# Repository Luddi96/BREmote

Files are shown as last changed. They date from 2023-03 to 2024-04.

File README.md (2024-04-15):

# BREmote - Open Source eFoil and Esk8 remote 
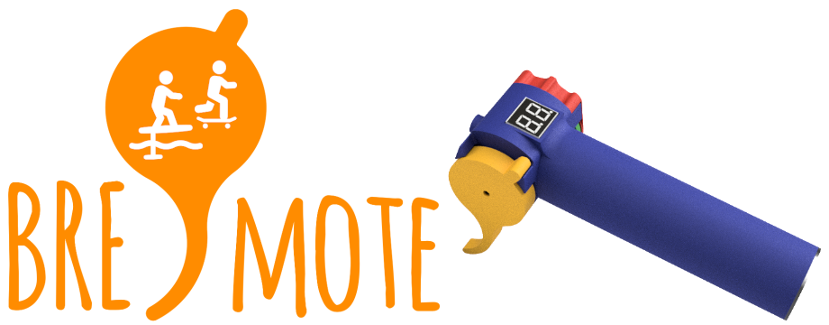
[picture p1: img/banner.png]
Banner


## Features:
* All mechanical parts 3D printed (even the springs)
* Symmetric design - left & right side can be swapped
* Sustainable - All external parts can be replaced
* Open Source: 3D Models, Electronics and Software are GPL3.0
* 2.4GHz Link (range dependant on antenna type, position)
* Communication with VESC via UART / CAN
* Low battery alarm (vibration)
* Water ingress alarm integrated in receiver
* Fall-off detection (not yet implemented)
* Gears / Power Levels / Cruise Control
* Charging and Programming via USB

## Links:
* [Promo Video](https://youtu.be/fF5BHrkHTNA)
* [Overview + Build Video](https://youtu.be/kb76z3FXLc0)
* [Updated Build Video](https://youtu.be/RKn8jVGVD6g)
* [Deep Dive Video](https://youtu.be/cdQ3Ppyngpk)
* [Update Video 04/2023](https://youtu.be/SpBOiRbGKgA)
* [Steering & Long Range Update Video](https://youtu.be/DhPk98Wdcn0)

## Parts needed:
### Electronics:
* [Tx & Rx PCBs, order at JLCPCB, Gerbers see releases](https://github.com/Luddi96/BREmote/releases)
	* [Instruction how to order at JLC (only do Step 2&4)](https://youtu.be/y3GviDr0o1s)
* [Tx wireless module "Color: NRF24L01 SMD"](https://de.aliexpress.com/item/1005004905334589.html)
* [Rx wireless module "Color: GT-24 SMD"](https://de.aliexpress.com/item/1005004905334589.html)
* [IPEX Antenna for Rx](https://de.aliexpress.com/item/1005003399563785.html)
* [0.36" 2-digit, 7-Segment Display, Common Cathode "CC"](https://de.aliexpress.com/item/32730115504.html)
* [2x SMD Header, 2x5-pin](https://de.aliexpress.com/item/32336498109.html)
* [EITHER Connector SP13 4-pin](https://de.aliexpress.com/item/1005001891060229.html)
* [OR Magnetic Connector](https://de.aliexpress.com/item/4001283688823.html)
* [Battery Sanyo UR14500AC 740mAh](https://www.nkon.nl/de/sanyo-ur14500ac-740mah-1-52a-reclaimed.html)
* [Vibration Motor 24x7mm, 3.7 to 5V](https://de.aliexpress.com/item/1005004063804397.html)

### Mechanics:
* [2x Magnet N52 D3x6mm](https://www.ebay.de/itm/162903572491?var=461969545239)
* [2x Self-Threading Screw DIN7982 2.2x6.5mm](https://www.ebay.de/itm/272909463518?epid=17007662352)
* [PU Foam, ~Factor 15, e.g. Talamex 45729200](https://www.boatcareshop.nl/bootverf-bootlak/talamex-pu-schuim-2-componenten-200-cc)
* [3D Printed Parts, see releases](https://github.com/Luddi96/BREmote/releases)

## Recommended Connector Pinning:
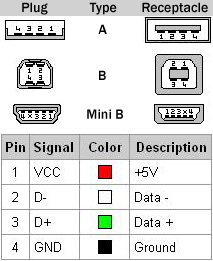
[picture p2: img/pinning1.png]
Pinning1
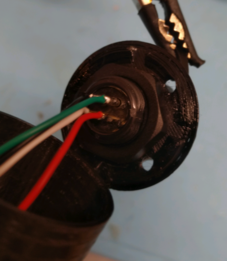
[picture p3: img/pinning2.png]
Pinning2
 

## Usage:
- With the remote off, push the toggle forward to turn it on
- As long as you keep the toggle forward, you will be shown the internal battery capacity in %
- With `//#define NO_LOCK` disabled in SHARED_CONFIG.h:
	- The remote will start in locked state
	- Push the toggle down to unlock
	- The remote will show you "PP", demanding you to push the trigger to its maximum position
	- Once you release the trigger, the remote will be in operating state
	- Push the toggle up/down to increase/decrease gear (The remote will always start in *lowest* gear)
	- Push and hold the toggle down to lock again
	- Push and hold the toggle up to turn off the remote
- With `#define NO_LOCK` enabled in SHARED_CONFIG.h:
	- The remote will immediately start in unlocked state
	- Push the toggle up/down to increase/decrease gear  (The remote will always start in *highest* gear)
	- Push and hold the toggle up to turn off the remote

## Status Codes:
| Symbol | Meaning |
| --- | --- |
| [] |System Locked |
| PP |Press Trigger once to arm |
| L0-L9 |Current "Gear", use Toggle to change |
| UU |Undervoltage, charge Battery |

## Error Codes:
| Err Code | Meaning | Potential Causes |
| --- | --- | --- |
| E3 | Packet Content Invalid | Unexpected data received, probably due to SW error or signal interference |
| E4 | No Ack | No acknowledgement from Receiver, signal too weak or signal interference |
| E5 | EEPROM Error | Unexpected/no calibration in EEPROM, try calibrating the remote again |
| E6 | NRF Module | NRF (Wireless) Module can't be initialized, probably hardware fault |
| E7 | Water Ingress | Water on the water detection electrodes attached to the receiver. This feature can be disabled in code if you dont use it (default: enabled). |
| E8 | BMS Fault | BMS has disabled its output connected to the receiver. This feature can be disabled in code if you dont use it (default: disabled). |

# Connection Examples:

<details>
<summary>VESC with UART</summary>

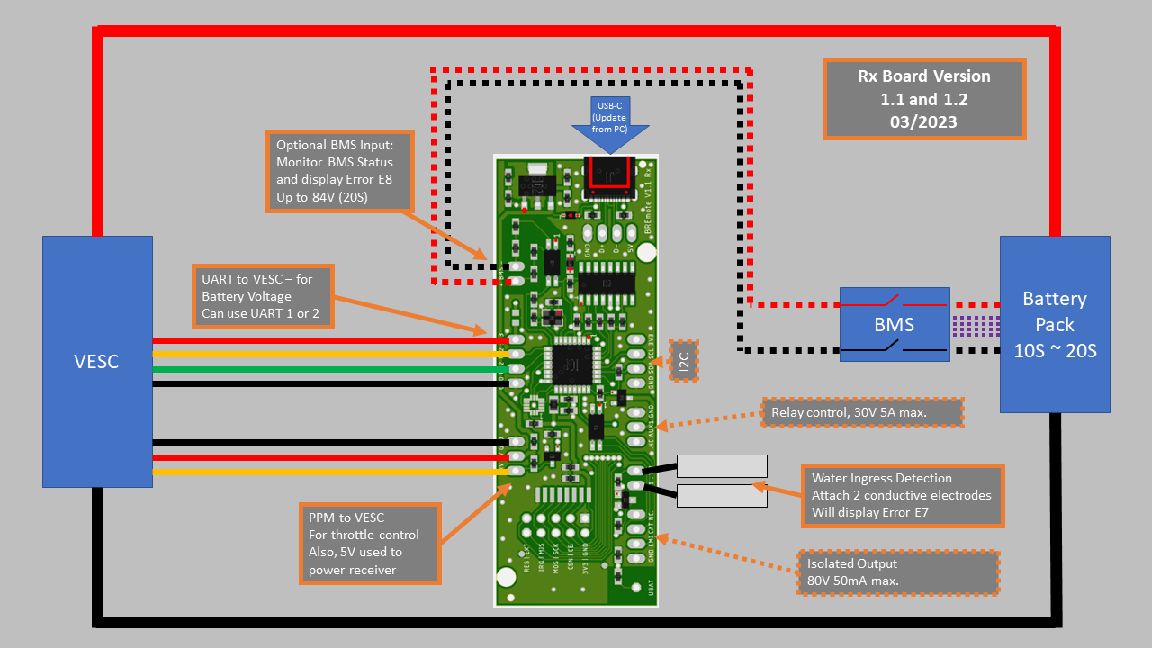
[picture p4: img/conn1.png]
Conn1


</details>

<details>
<summary>ESC or VESC WITHOUT UART</summary>

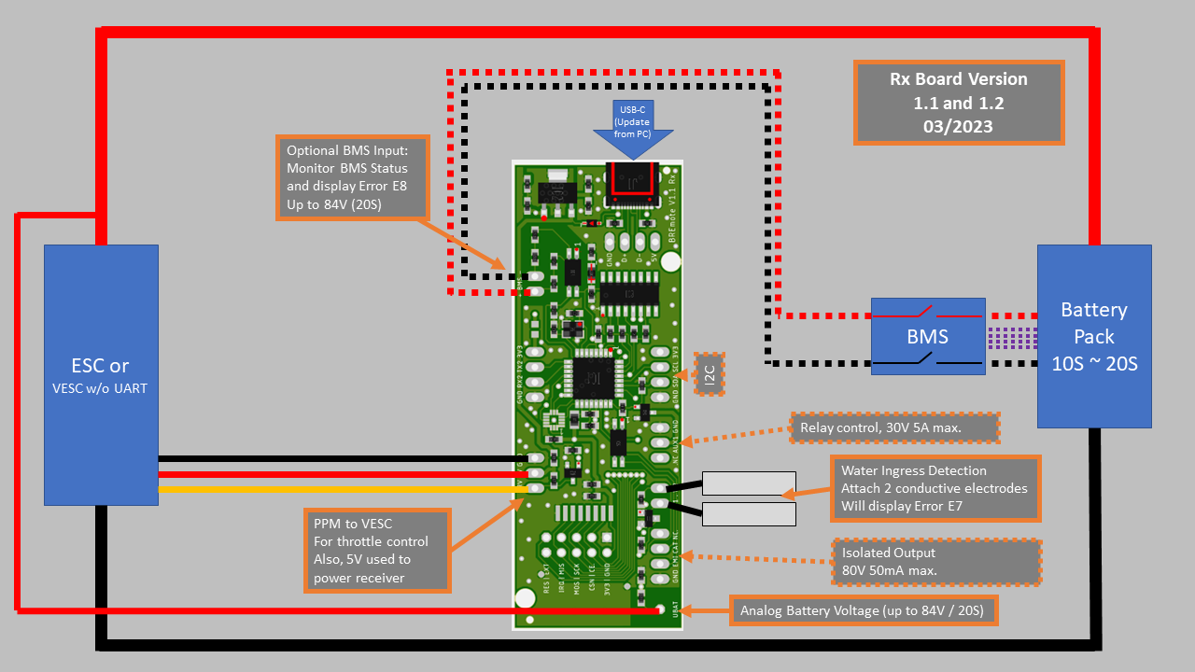
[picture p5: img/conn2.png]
Conn2


</details>

<details>
<summary>Steering/Dual Motor</summary>

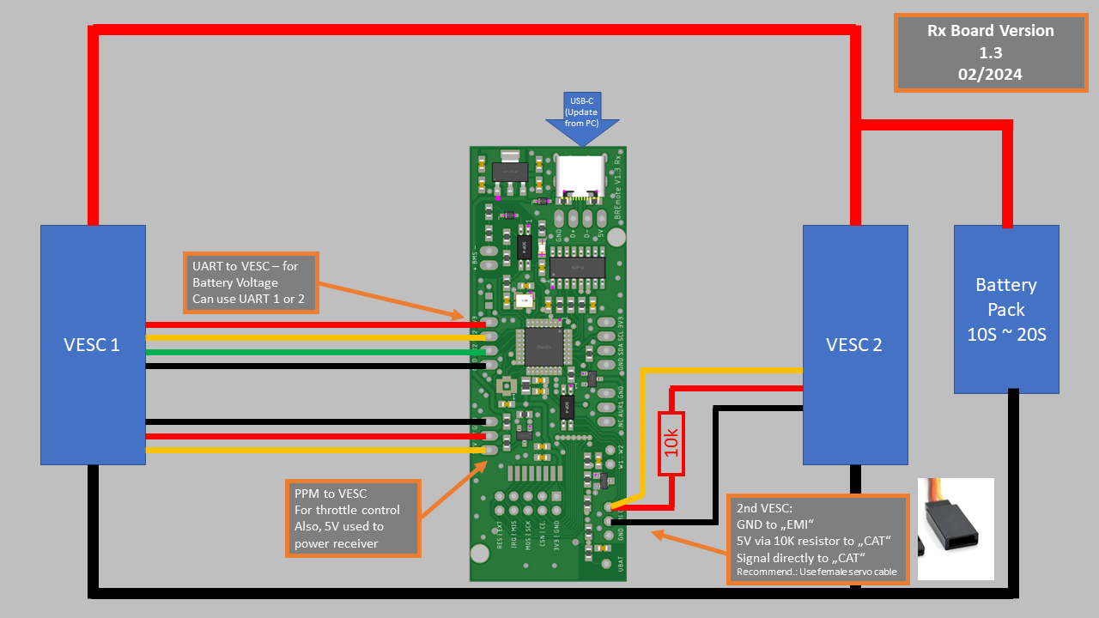
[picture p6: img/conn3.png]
Conn3


</details>

---
# FAQ:
Q: When trying to program the remote with the Arduino IDE, I get an error "avrdude: stk500_getsync()"
A: Make sure you selected "Arduino Nano ATmega328P **(Old Bootloader)**"

---
# Changelog:
### 2024-04-15: [Release V1.7]
Note: Changing to this release will require new calibration!
### 2024-04-15: [Source - all]
- Tx:
	- THR_TO_PWRUP: Remote can be set to only turn on when throttle is pressed (more robust to unwanted turn-on)
	- REVERSE: Instead of 10 forward gears, there is a forward and reverse gear 
	- DONT_SEND_IDLE: Remote will stop sending packets when trigger is not pressed (multiple remotes can be used with one Rx, e.g. for sharing a tow boogie)
- Rx:
	- Diff. Steering
- Calibration:
	- Added new paramter for "THR_TO_PWRUP" function
- Add connection example for Steer/Dual Motor
### 2023-12-28: [Release V1.6.4]
### 2023-12-28: [Mechanics - LR]
- Minor changes on main body
	- Longer antenna hole (now 58mm)
	- Reinforcements
### 2023-06-01: [Release V1.6.3]
### 2023-10-02: [Mechanics - LR]
- Added Juergens improved version of the long range bodies
### 2023-06-01: [Release V1.6.2]
### 2023-10-02: [Source - Tx]
- Softer Gears: When at full throttle, changing gear is smoothened (Thanks to Dyse)
### 2023-07-24: [Source - Readme]
- Added Information how to connnect ISP for LR version
### 2023-06-01: [Release V1.6]
### 2023-06-01: [Source]
- Remove Toto Mode
- Add more options to customize UI:
	- NO_LOCK
	- NO_POWERBUTTON
	- NO_GEARS
- Add temperature display
### 2023-05-05: [Release V1.5.1]
### 2023-05-05: [Source - Tx]
- Added "Toto mode" (less filtering for another throttle sensing concept)
- Disable Lock & Poweroff when riding (when throttle is engaged)
### 2023-04-23: [Release V1.5]
### 2023-04-23: [Source]
- Added Steering Function (see [update video](https://youtu.be/DhPk98Wdcn0) )
### 2023-04-23: [Electronics - Tx]
- Added longrange (LR) version of Tx board (uses same NRF module like Rx)
### 2023-04-14: [Release V1.4.2]
### 2023-04-14: [Source]
- Set MOSI Pin to "Input" in standby (Critical fix, as this could damage battery)
### 2023-04-14: [Source]
- Add compiler error if address is not changed
- Increase tolerances on some values
### 2023-04-14: [Release V1.4.1]
### 2023-04-14: [Source - Rx]
- Increased NRF interrupt-to-readout delay
### 2023-03-31: [Release V1.4]
### 2023-03-31: [Readme]
- Added connection diagrams
### 2023-03-31: [Source]
- Made connection to VESC UART optional (defined in SHARED_CONFIG)
- Added analog UBAT measurement
### 2023-03-31: [Electronics - Rx]
- Added component to make analog UBAT measurement more resitant to electromagnetic disturbance
### 2023-03-30: [Source]
- Add error timeout, to allow user to change gear during an error
### 2023-03-12: [Release V1.3]
### 2023-03-20: [Electronics - Rx]
- Added components to make Water Ingress Detection (Wetness Sensor) more resitant to electromagnetic disturbance
### 2023-03-20: [Source]
- Added BMS monitoring function
- Fixed Water Ingress Detection (Wetness Sensor) functionality
### 2023-03-12: [Release V1.2]
### 2023-03-12: [Source]
- Added more information, which Board and Processor to select for programming with Arduino IDE
- Renamed Source Files to not contain Version anymore
- Added Water Ingress Detection (Wetness Sensor) functionality
### 2023-03-07: [Release V1.1]
### 2023-03-04: [Electronics - Tx]
- Made Board 1mm smaller (each 0.5mm from top/bottom)
- Therefore shifted SPI vias and some other traces, changed style of motor pinheaders
### 2023-03-04: [Source]
- Found a error which depleated the battery in standby mode.
- Changed System.ino : disablePower() routine
### 2023-01-20: [Mechanics]
- Added Trigger Opitions with -15 and -30°
- Made Selector Rotator and Selector Spring thinner
- Updated "AllTheSmallThings"
### 2022-12-30: [Mechanics]
- Added Trigger spring with 1mm thickness (before: 1.2mm could lead to spring not being able to "roll in" all the way)
### 2022-12-02: [Electronics - Rx]
- Added protection diode to BMS measurement
### 2022-11-06: [Electronics - Tx]
- Better GND Connection for NRF Module
- Corrected Battery Polarity in whiteprint
- Added Diode to VREF
- Changed Reset to SMD Pad

---
# Credits:
Logo uses "watersport" and "Skate" by Adrien Coquet from https://thenounproject.com/. CC BY 3.0.

Thanks to Daniel for implementing and testing the magnetic connector!
Tanks to Dyse for implementing the soft gears feature!
Thanks to Juergen for the improved long range bodies!

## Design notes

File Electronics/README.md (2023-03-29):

## Note:
Before soldering NRF Module in Place, upload Bootloader to Boards. For that, see Source Readme.

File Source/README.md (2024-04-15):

## How to upload bootloader
Before you can use Arduino IDE to flash the firmware, you need to upload the bootloader to the BREmote once!
For that, you need an AVR ISP or another Arduino.

Note: You should do this, before soldering the NRF Module in place. Just take 6 wires and solder them directly to the pads. Upload bootloader and verify success. Afterwards, desolder the wires and solder NRF module into place.

Note: If you have the accelerometer populated, flashing should be done at 3.3V (Arduino has 5V), you should use a level shifter on all SPI pins to avoid damage to the accelerometer IC.

Note: The Pinout is only valid for the "normal" Tx Version. For the Tx_LR (long range), please contact me.

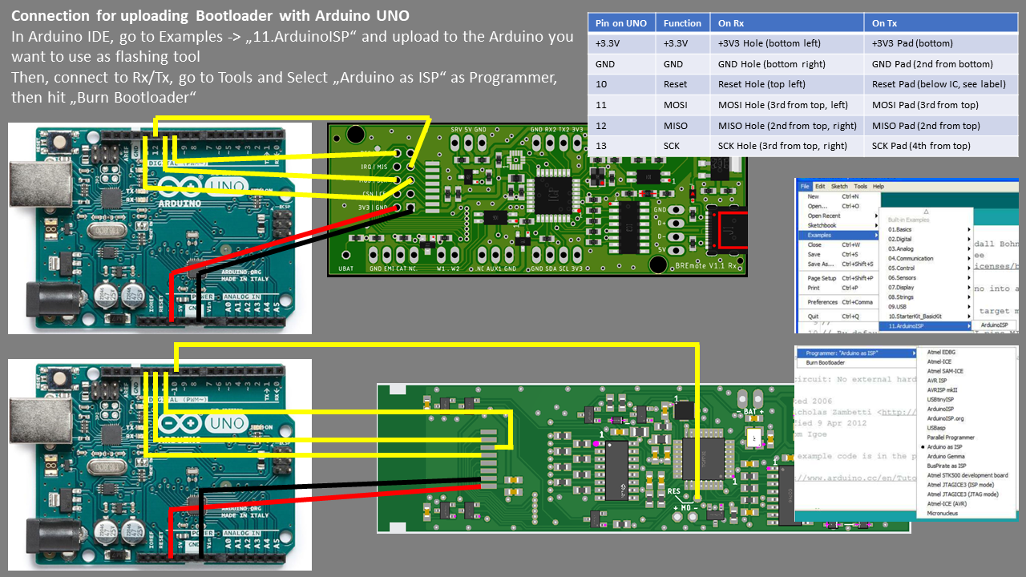
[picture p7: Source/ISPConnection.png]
ISP

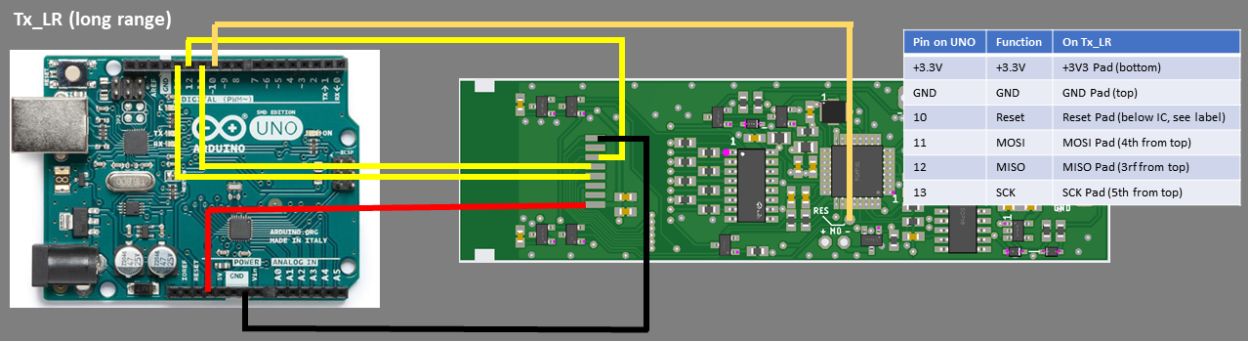
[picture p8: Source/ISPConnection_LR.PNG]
ISP_LR


## How to compile / upload

Download Arduino IDE.
In Arduino IDE, go to Sketch -> Add Library -> Search for "RF24" and Install "RF24" from TMRh20 (you'll need to scroll down a bit).

Board

If the upload does not work, select as Board "Arduino Nano (ATMEGA328P) (OLD BOOTLOADER)"

## Software Changes
These are the most frequent changes in "SHARED_CONFIG.h":
Change this in BOTH the Tx and Rx directory!
```
uint8_t rxAddr[6] = {"BREAI"}; //From Rx To Tx (Board to Remote)
uint8_t txAddr[6] = {"BREAO"}; //From Tx To Rx (BRemote to Board)
```
* For the adresses, choose any 5-character strings you want. Make sure it is unique for everybody using a BREmote at the same time.
```
#define NO_LOCK
```
* If "NO_LOCK" is uncommented, the remote will start locked and with Powerlevel 0 as default. "NO_LOCK" will deactivate locking & start at Powerlevel 9.
```
#define FOIL_BAT_EMPTY_AT 180 //10*V (e.g. 200 = 20V)
#define FOIL_BAT_FULL_AT 220  //10*V (e.g. 200 = 20V)
```
* "FOIL_BAT_xx" will define at which voltage the VESC battery is recognized as full or empty.
This change is made in the config of Rx! DO NOT change the INT_VBAT_xx in Tx!
This is in 10*Voltage, Example values (2.5V/4.2V):

| Series Pack | EMPTY_AT | FULL_AT |
| --- | --- | --- |
| 10S | 250 | 420 |
| 12S | 300 | 504 |
| 14S | 350 | 588 |
| 16S | 400 | 672 |
| 18S | 450 | 756 |
| 20S | 500 | 840 |

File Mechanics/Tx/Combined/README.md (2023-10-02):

## Print settings:
- All parts are already in correct orientation for printing!
- Only Main_Body needs support.
- Nozzle Dia 0.4mm
- Layer Height 0.2mm
- First Layer 0.3mm
- 3 outer layers
- PETG recommended.

## What to do:
- Print "AllTheSmallThings", Handle, MainBodies.
- Trigger:
	- There are 3 trigger angles, see image below
	- Righthander: Print Trigger once
	- Lefthander: Mirror Trigger and print once
- Print "AllTools" for easier assembly

These are the different trigger angles:
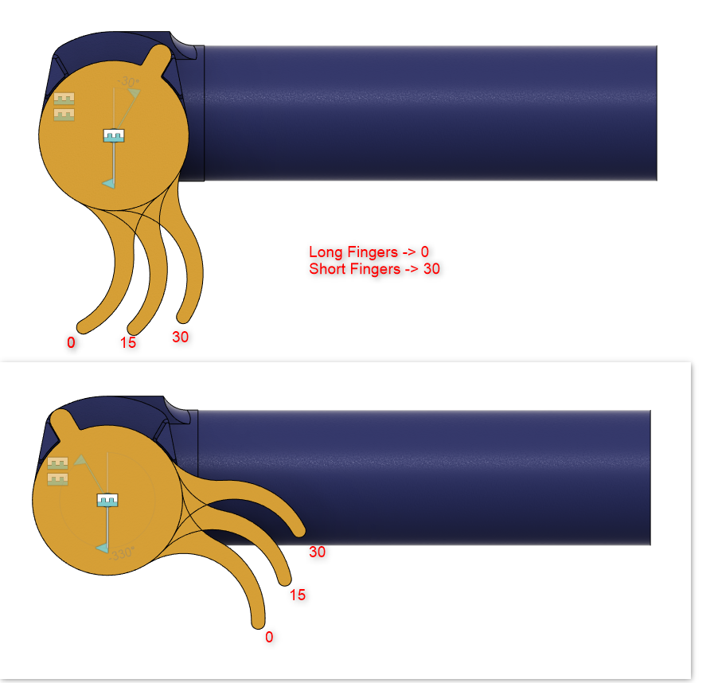
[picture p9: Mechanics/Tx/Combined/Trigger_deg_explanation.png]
Image of different trigger angles


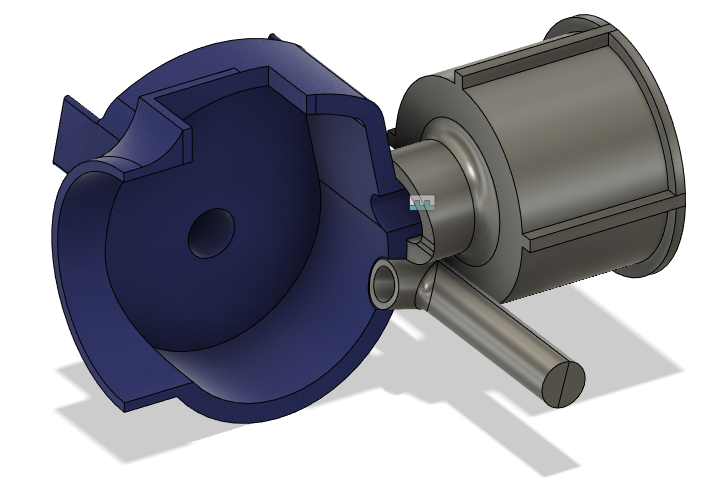
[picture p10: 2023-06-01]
Mechanics/Tx/Long_Range/2023-05-06_13h26_05.png

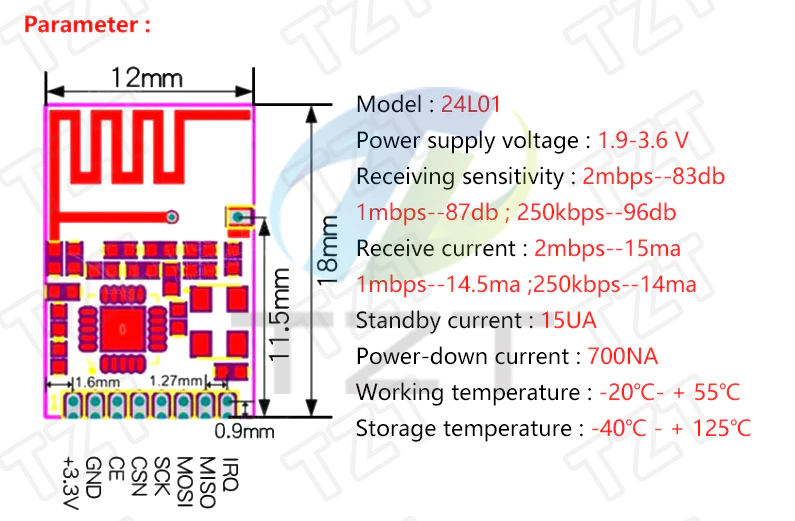
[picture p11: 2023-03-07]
Electronics/Datasheets/Tx_Module.png

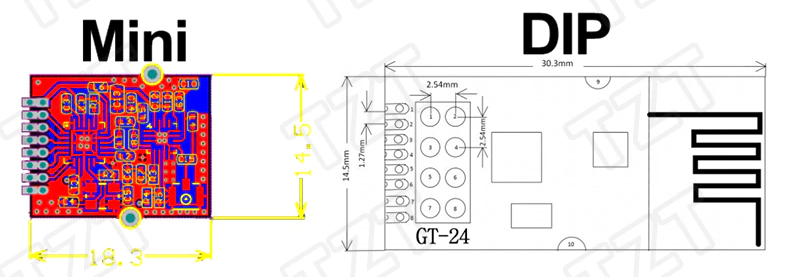
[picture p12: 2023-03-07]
Electronics/Datasheets/Rx_1.png

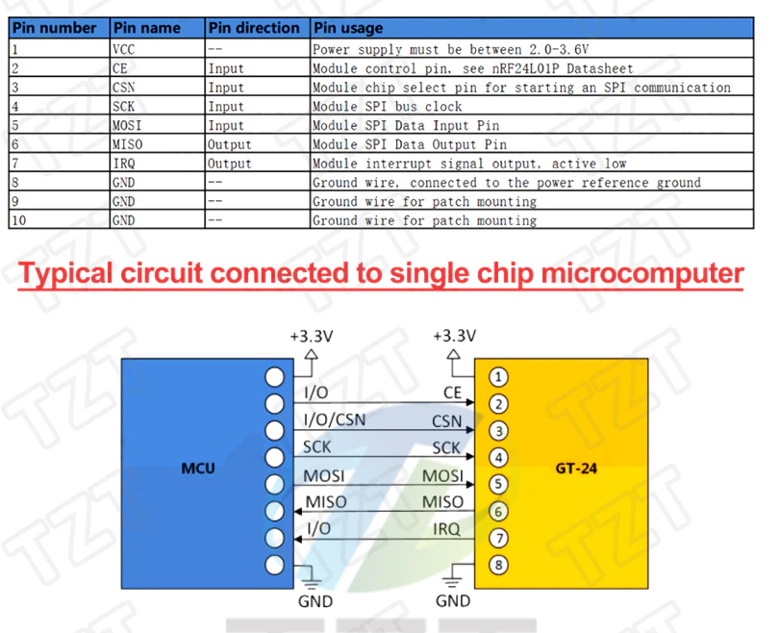
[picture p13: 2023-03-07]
Electronics/Datasheets/Rx_2.png

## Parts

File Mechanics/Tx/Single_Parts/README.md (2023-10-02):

## Print settings:
- All parts are already in correct orientation for printing!
- Only Main_Body needs support.
- Nozzle Dia 0.4mm
- Layer Height 0.2mm
- First Layer 0.3mm
- 3 outer layers
- PETG recommended.

## What to do:
- Parts without numbers at the end, print 1 times
- Parts with _2x, print 2 times
- Parts with _2m, print once and once mirrored (MagRodCover and MainBody)
- For the MagRodStopper, there are 4 lenghts, try with _+02_default
	- If too tight -> use _+04, if too lose -> use _00 or _-02
- Trigger:
	- There are 3 trigger angles, see image below
	- Righthander: Print Trigger once
	- Lefthander: Mirror Trigger and print once
- Or just use the combined .stl in the "Combined" folder

These are the different trigger angles:
Image of different trigger angles

Special thanks to Daniel for designing and testing the "HandleBackCap_Mag"

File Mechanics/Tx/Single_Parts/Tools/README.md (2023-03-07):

Note: Please remove AssemblyHelper Top and Bottom after glueup (they don't belong on the final remote)

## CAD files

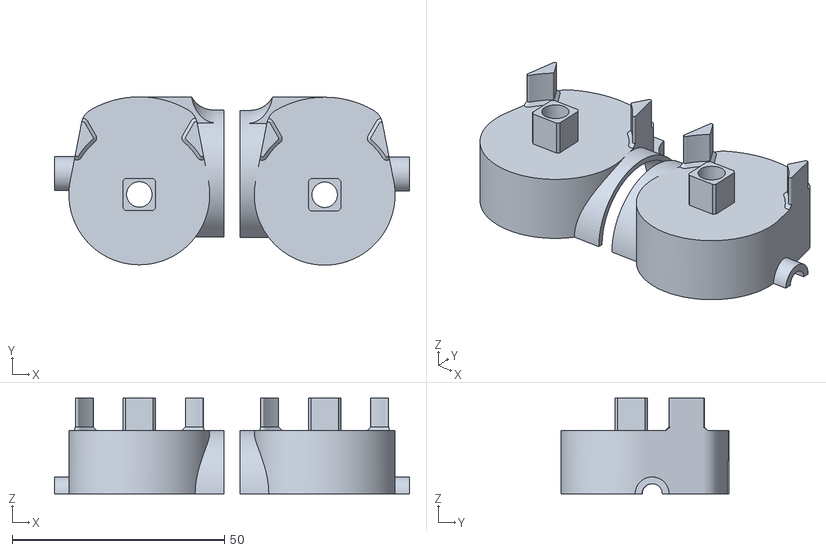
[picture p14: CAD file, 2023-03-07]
Mechanics/Tx/Combined/MainBodies.stl
83.7 x 39.7 x 22.6

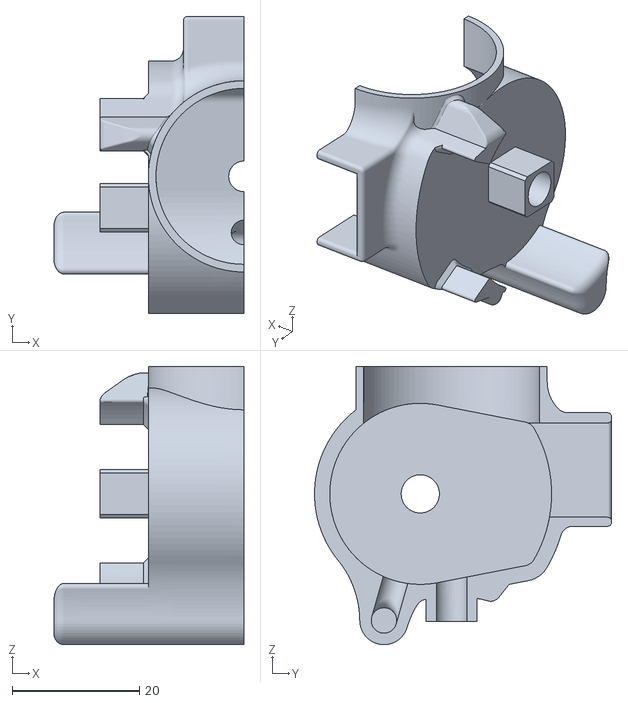
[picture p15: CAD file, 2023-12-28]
Mechanics/Tx/Long_Range/main_body_left_normal.stl
29.8 x 46.6 x 43.7

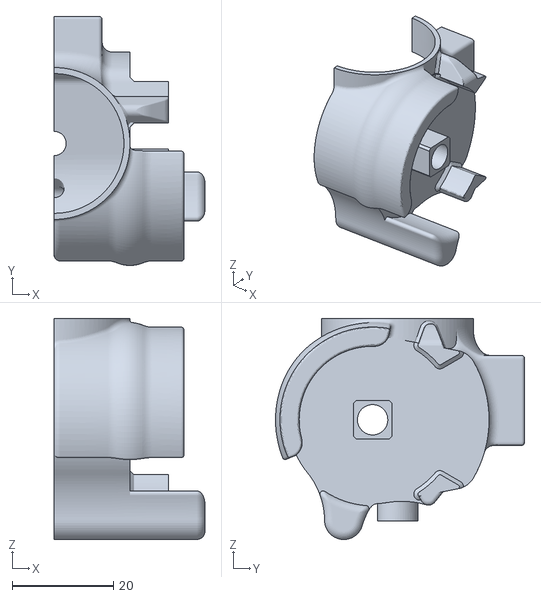
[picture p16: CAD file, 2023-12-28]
Mechanics/Tx/Long_Range/main_body_right_toggle_protection.stl
29.8 x 49.2 x 43.7

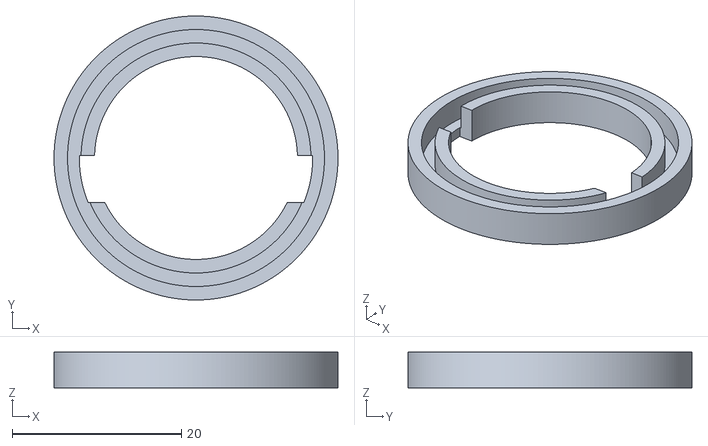
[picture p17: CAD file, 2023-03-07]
Mechanics/Tx/Single_Parts/Tools/AssemblyHelperBottom.stl
33.6 x 33.6 x 4.20

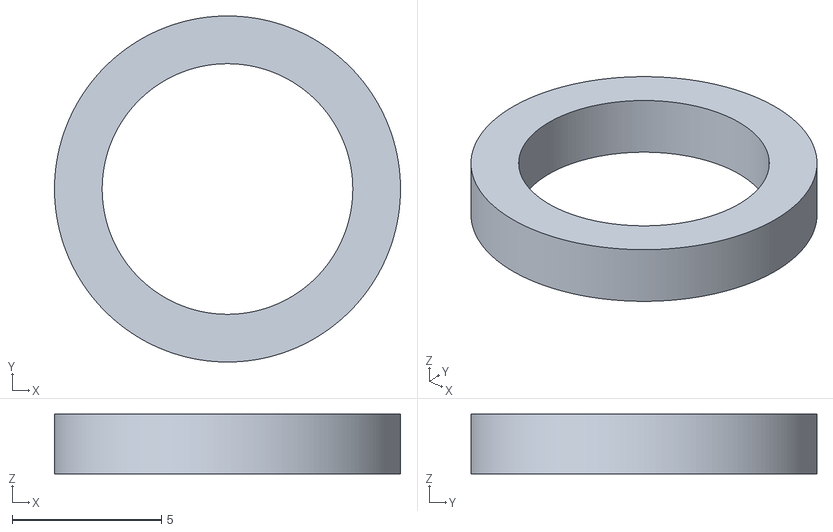
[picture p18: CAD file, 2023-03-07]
Mechanics/Tx/Single_Parts/Tools/AssemblyHelperTop.stl
11.6 x 11.6 x 2.00

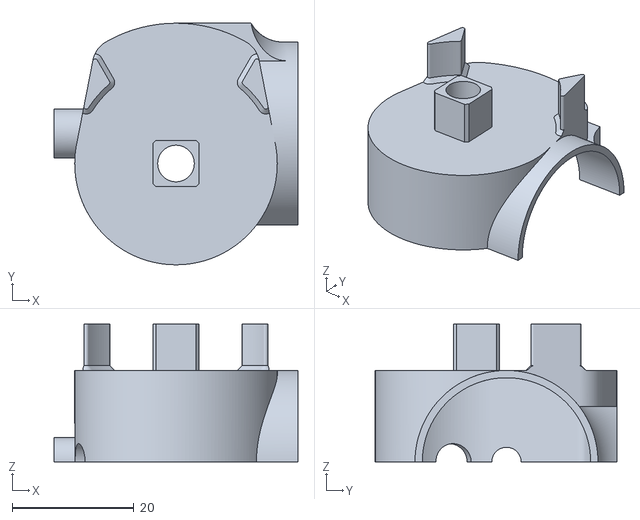
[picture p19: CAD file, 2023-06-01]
Mechanics/Tx/Long_Range/MainBody_Left_2m.stl
40.0 x 39.6 x 22.6

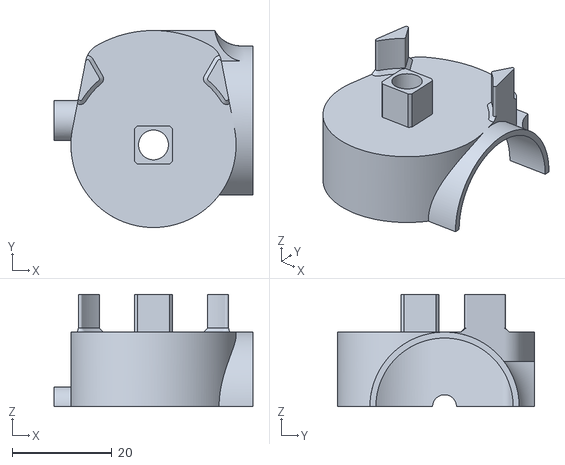
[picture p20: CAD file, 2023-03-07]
Mechanics/Tx/Single_Parts/MainBody_Left_2m.stl
40.0 x 39.6 x 22.6

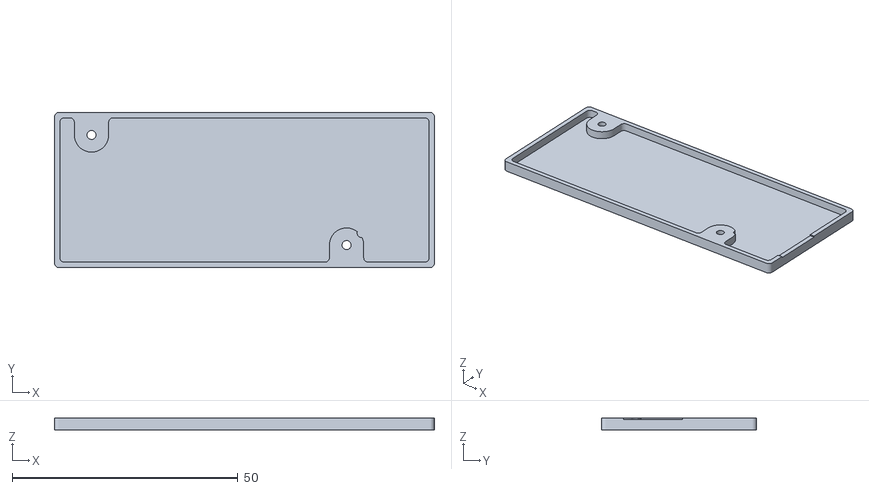
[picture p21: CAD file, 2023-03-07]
Mechanics/Rx/Bottom.stl
84.2 x 34.4 x 2.70

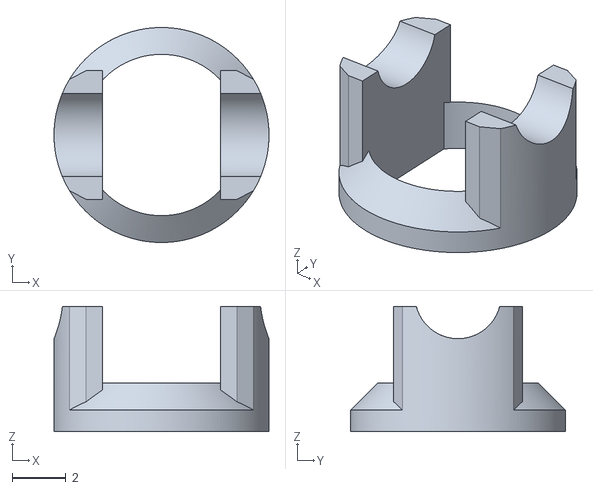
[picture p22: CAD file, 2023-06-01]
Mechanics/Tx/Single_Parts/MagRodStopper_00_less_2x.stl
8.00 x 8.00 x 4.66

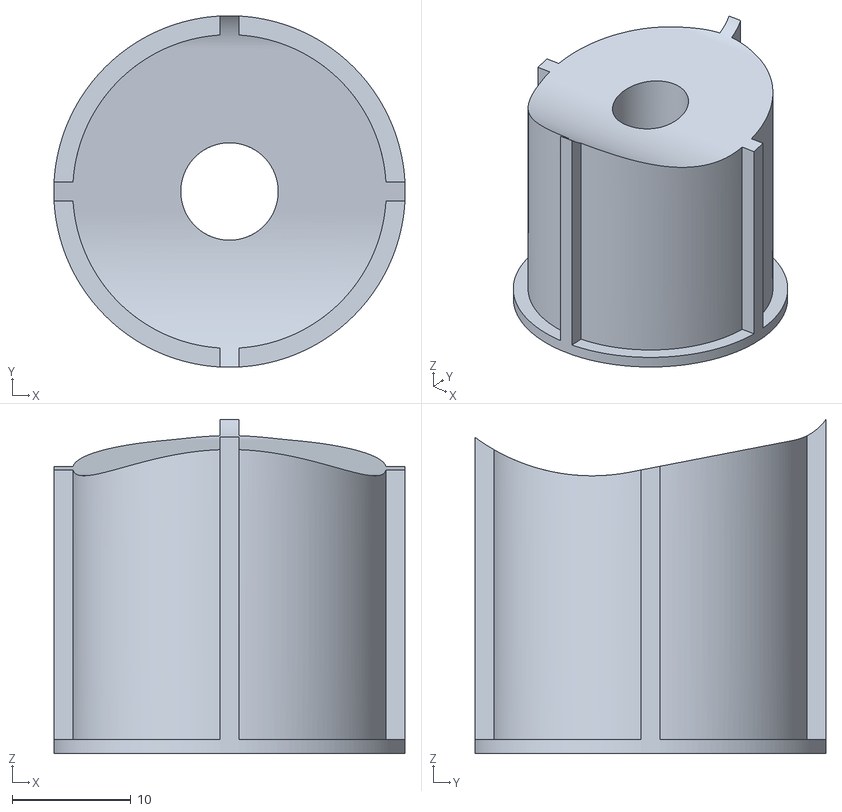
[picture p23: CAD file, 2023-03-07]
Mechanics/Tx/Single_Parts/Tools/PushRod.stl
29.6 x 29.6 x 28.2

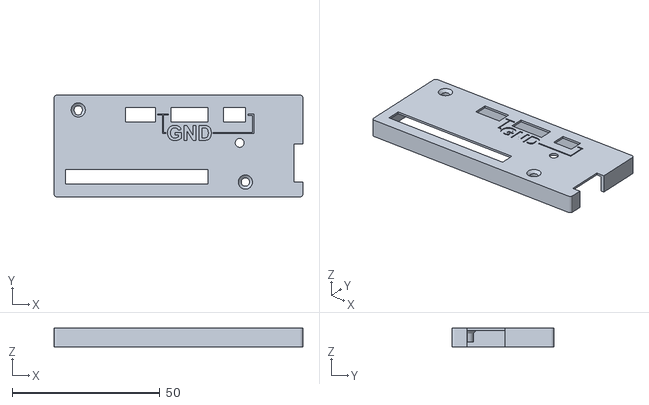
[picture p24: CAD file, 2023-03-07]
Mechanics/Rx/Top.stl
84.2 x 34.4 x 6.27

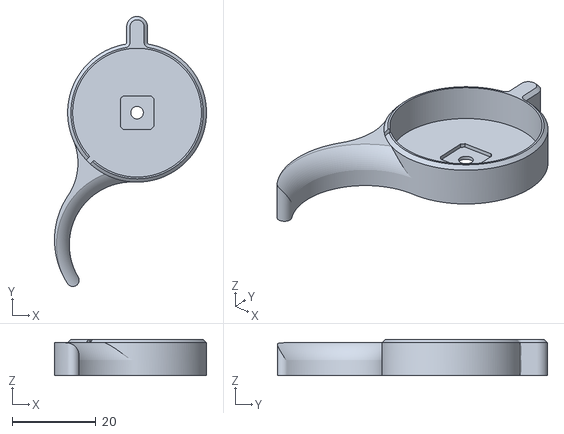
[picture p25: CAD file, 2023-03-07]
Mechanics/Tx/Combined/Trigger_0deg.stl
36.3 x 64.6 x 8.70

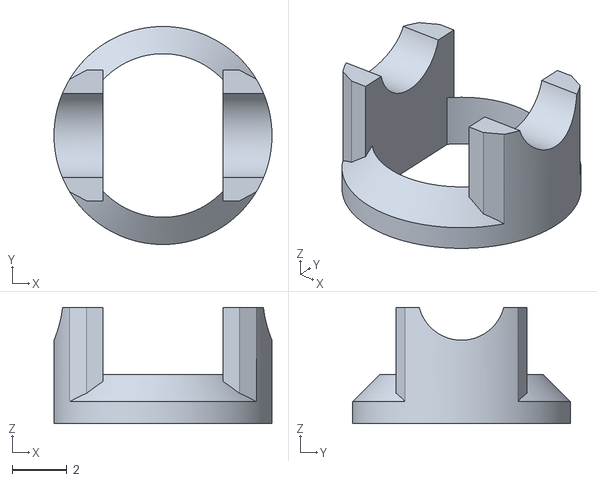
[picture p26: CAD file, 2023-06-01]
Mechanics/Tx/Single_Parts/MagRodStopper_+04_more_2x.stl
8.00 x 8.00 x 4.26

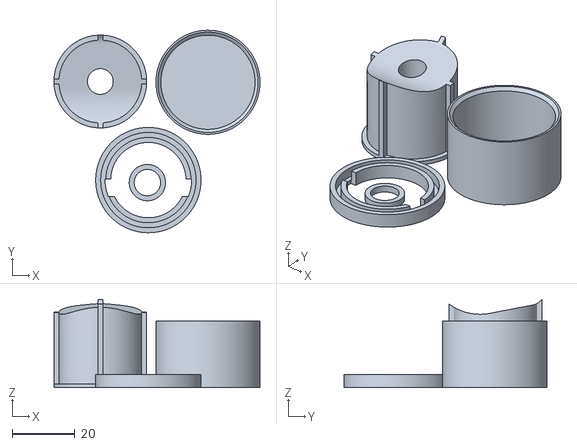
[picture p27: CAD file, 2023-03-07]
Mechanics/Tx/Combined/AllTools.stl
65.7 x 64.6 x 28.2

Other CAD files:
Mechanics/Tx/Long_Range/Special_Pushrod.stl
Mechanics/Tx/Single_Parts/MagRodStopper_-02_less_2x.stl
Mechanics/Tx/Single_Parts/Tools/MixCup.stl
Mechanics/Tx/Combined/Handle.stl
Mechanics/Tx/Combined/AllTheSmallThings.stl
Mechanics/Tx/Combined/Trigger_15deg.stl
Mechanics/Tx/Combined/Trigger_30deg.stl
Mechanics/Tx/Long_Range/Antenna1.stl
Mechanics/Tx/Long_Range/Antenna2.stl
Mechanics/Tx/Long_Range/old_design/Antenna1.stl
Mechanics/Tx/Long_Range/old_design/Antenna2.stl
Mechanics/Tx/Single_Parts/FillportCover.stl
Mechanics/Tx/Single_Parts/HandleBackCap_Mag.stl
Mechanics/Tx/Single_Parts/HandleBackCap_SP13.stl
Mechanics/Tx/Single_Parts/Handle_100mm.stl
Mechanics/Tx/Single_Parts/MagRodCover_Left_2m.stl
Mechanics/Tx/Single_Parts/MagRodStopper_+02_default_2x.stl
Mechanics/Tx/Single_Parts/MagRod_2x.stl
Mechanics/Tx/Single_Parts/SelectorArm_Bothsides.stl
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

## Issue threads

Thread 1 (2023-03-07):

[Feature Request]: Implement water ingress detection into Rx Source

Luddi96, 2023-03-07:
TODO: Use the existing pin designed for water ingress detection, read it out and send it via the error code byte to the Remote

Luddi96, 2023-03-12:
Resolved in 9b4daf09fd37b46db3c2a3dd7a2333e4f6e3bf7d

Closed 2023-03-12.

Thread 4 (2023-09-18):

[FEATURE REQUEST]: Autopilot

jensutbult, 2023-09-18:
Use the IMU in the RX to steer e.g a tow boogie. Instead of controlling differential thrust or a rudder with the remote, using the select button on the remote will change the heading which the autopilot use to steer the tow boogie. The speed of change of heading will preferably be proportional to how far you pull the lever. By default the autopilot will be off to allow for normal steering via the tow line but as soon as the user turns the select button while throttle is on it will be engaged. The autopilot is disengaged when the throttle is turned to zero again.

This will make it a lot easier to use a tow boogie in waves or simply to practice pumping in flat water. When the user wants to let go of the tow boogie he simply turns the select button while the tow boogie is running. This will engage the autopilot and the tow boogie will keep tracking straight even if waves or wind tries to knock it off course. If the user wants to adjust the heading of the tow boogie steering works very similar to the current implementation but instead of controlling a rudder it will update the internal heading to which the autopilot is trying to steer.

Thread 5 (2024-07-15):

[BUG]: UART not working with VESC 6.0.2 and MKS 75200

patatman, 2024-07-15:
**Describe the bug**
When enabling UART I'm getting the error in the serial monitor:
`Message Error`

For some reason UART won't work. I've soldered TX2 and RX2 to the corresponding RX2 and TX2 on the Bremote receiver, but it won't work.
I've now directly connected the battery to the Receiver so I can see the battery % anyway.

But UART would be intresting, since I can also monitor temperature.

Any idea what it could be?
I've wired the TX to RX and RX to TX.
Baudrate is at 15200

Luddi96, 2024-07-15:
Try connecting TX to TX, Rx to Rx. Please report back if that works.

patatman, 2024-08-25:
Sorry I never responded, I fixed it by using the PPM.
So didn't get around resoldering it. You can close this if you'd like.
Won't be until the winter until I start switching components again

Luddi96, 2024-08-25:
No problem. I will close and you can open a new one should the problem persist

Closed 2024-08-25.

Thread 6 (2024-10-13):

Standard arduino for receiver?

yifeim, 2024-10-13:
Hi,

For people who burned their receivers due to voltage spikes, is it possible to rebuild the receiver using standalone arduino-nano + gt-24 parts? I just need the basic functions to convert radio signal to pwm. Also, I would like to use a separate power source to avoid voltage spikes from the motor end. Thanks!

Luddi96, 2024-10-13:
Hey,
That is possible in principle
However a normal Arduino runs on 5V, the GT24 needs 3.3V so you will have to either add a level shifter or convert the Arduino to 3.3V
Also the PWM output needs a transistor and a few additional components.
You can check out the schematic and compare with an Arduino to see what needs to be added or changed

yifeim, 2024-10-13:
Thank you. Which file should I look at and what software to open it with?

Luddi96, 2024-10-13:
In the Schematic folder, download the .sch file
It can be viewed with Autodesk Eagle or a free online viewer like this one
https://www.pcbway.com/tool/ElectronicDesignViewer

yifeim, 2024-10-14:
Thank you! It's definitely interesting to read through the designs. I think
it might be possible to drive the esc pwm directly through the controller
pin (with some software inversion logic) and, as for 3.3v, we can add a
small led as a power step.

FYI, my board healed itself despite missing the accelerometer, so I am
replying just to learn.

LudwigBre ***@***.***> 于2024年10月13日周日 13:28写道：

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

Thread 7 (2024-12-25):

[FEATURE REQUEST] Temperature allert

StefanGas, 2024-12-25:
I have my ECS in the same box like the receiver.
The ESC has a temperature shutdown at 100°C.
This is suitable for drones and aircrafts with good air cooling but not inside the same box like the battery.
An early temperature allert would be great to know that the temperature in the box is rising and I should give it some time to cool down.
(I use no BMS and I did not found a way to set the temperature for the ESC lower)

I hope that some of the fancy chips on the receiver board has a temperature sensor on board 😁

Luddi96, 2024-12-25:
Hey there,
I can add this in the future
Until then you can add it yourself

Go to the System.h file of the TX firmware
All the way in the end you should see the following

`void checkBattery()
{
  calcInternalBattery();
  if(internal_battery < 20)
  {
    blinkDot |= 0x01;
  }
  else
  {
    blinkDot &= 0xFE;
  }

  if(vesc_battery < FOIL_VBAT_WARN_AT)
  {
    blinkDot |= 0x02;
  }
  else
  {
    blinkDot &= 0xFD;
  }

  if(internal_battery < 10)
  {
    poweroff = 1;
  }
}`

Modify the 2nd last if() like following (the value 80 is the desired temperature in °C)
To test if it works first set it to 20°C or something and see if the alarm goes off

if(vesc_battery < FOIL_VBAT_WARN_AT **|| vesc_temp > 80**)

StefanGas, 2024-12-26:
Hi,thanks for the quick reply.Is it possible to measure the temperature in the box with the receiver?I don't have a VESC.Best regards--Am 25.12.24, 18:19 schrieb LudwigBre ***@***.***>:

Hey there,
I can add this in the future
Until then you can add it yourself
Go to the System.h file of the TX firmware
All the way in the end you should see the following
`void checkBattery()
{
calcInternalBattery();
if(internal_battery < 20)
{
blinkDot |= 0x01;
}
else
{
blinkDot &= 0xFE;
}
if(vesc_battery < FOIL_VBAT_WARN_AT)
{
blinkDot |= 0x02;
}
else
{
blinkDot &= 0xFD;
}
if(internal_battery < 10)
{
poweroff = 1;
}
}`
Modify the 2nd last if() like following (the value 80 is the desired temperature in °C)
To test if it works first set it to 20°C or something and see if the alarm goes off
if(vesc_battery < FOIL_VBAT_WARN_AT || vesc_temp > 80)

—Reply to this email directly, view it on GitHub, or unsubscribe.You are receiving this because you authored the thread.Message ID: ***@***.***>

Luddi96, 2024-12-27:
Not without adding an additional sensor and quite a bit of code

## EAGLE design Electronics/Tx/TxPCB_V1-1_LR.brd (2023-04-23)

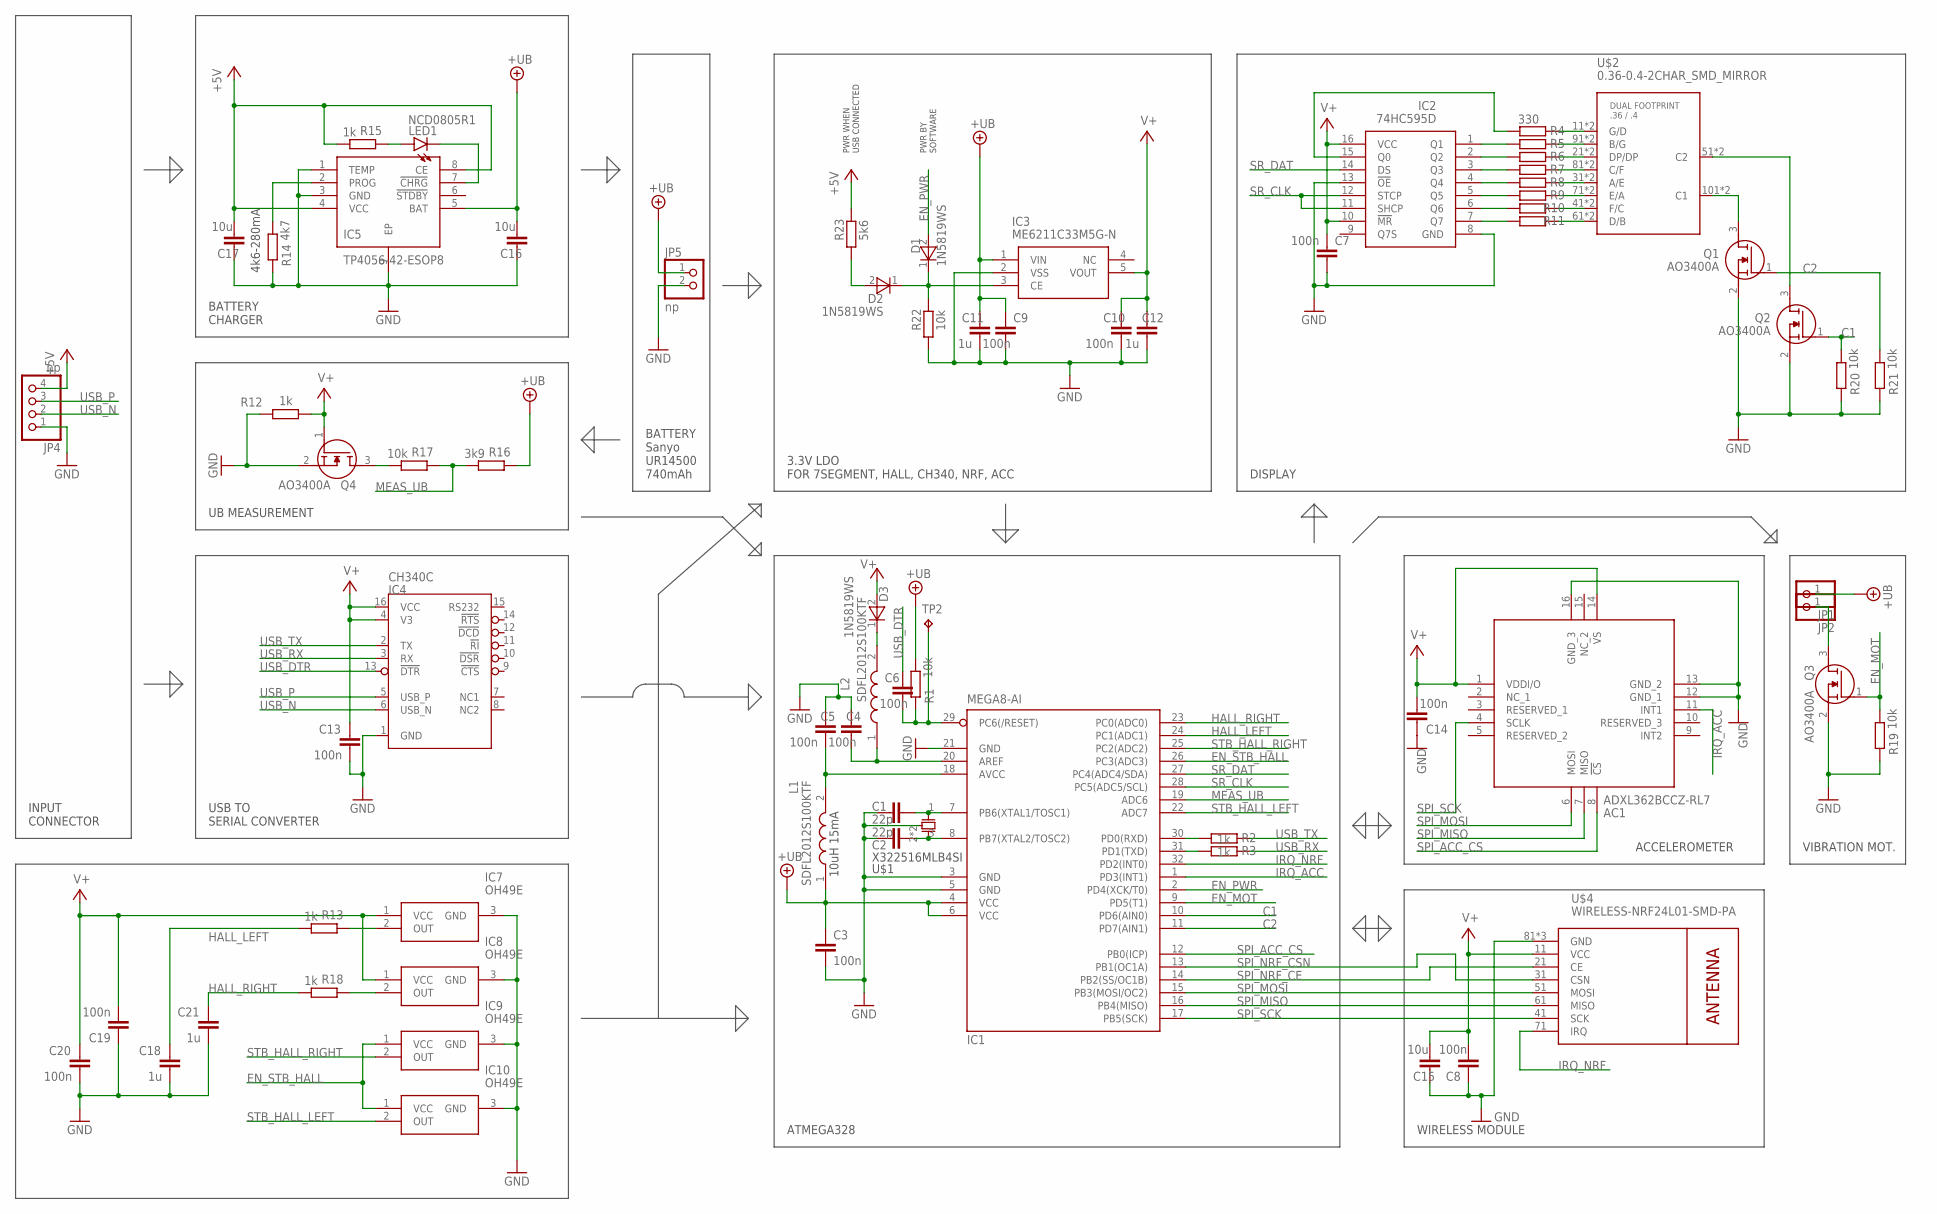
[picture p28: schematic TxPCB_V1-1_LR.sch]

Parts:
AC1: ADXL362BCCZ-RL7; CC-16-4
C1, C2: 22p; C0603
C3, C4, C5, C6, C7, C8, C9, C10, C13, C14, C19, C20: 100n; C0603
C11, C12, C18, C21: 1u; C0603
C15, C16, C17: 10u; C0603
D1, D2, D3: 1N5819WS; SODFL2512X90N
IC1: MEGA8-AI; TQFP32-08
IC2: 74HC595D; SOIC127P600X175-16N
IC3: ME6211C33M5G-N; SOT95P282X145-5N
IC4: CH340C; SOIC16N
IC5: TP4056-42-ESOP8; SOIC127P600X175-9N
IC7, IC8, IC9, IC10: OH49E; SOT95P237X112-3N
JP1, JP2: PINHD-1X1; 1X01
JP4: np; 1X04
JP5: np; 1X02
L1, L2: SDFL2012S100KTF; INDC2112X105N
LED1: NCD0805R1; CHIP-LED0805
Q1, Q2, Q3, Q4: AO3400A; SOT95P280X125-3N
R1, R17, R19, R20, R21, R22: 10k; R0603
R2, R3, R12, R13, R15, R18: 1k; R0603
R4, R5, R6, R7, R8, R9, R10, R11: 330; R0603
R14: 4k7; R0603
R16: 3k9; R0603
R23: 5k6; R0603
TP2: TPB1,27; B1,27
U$1: X322516MLB4SI
U$2: 0.36-0.4-2CHAR_SMD_MIRROR; COMBO-036-04_SMD
U$4: WIRELESS-NRF24L01-SMD-PA; WIRELESS-NRF24L01_SMD_PA

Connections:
+5V: C17.1, IC5.4 (VCC), IC5.8 (CE), JP4.4, R15.2, R23.2
+UB: C3.1, C9.1, C11.1, C16.1, IC1.4 (VCC), IC1.6 (VCC), IC3.1 (VIN), IC5.5 (BAT), JP1.1, JP5.1, L1.1, R1.2, R16.1
C1: IC1.10 (PD6(AIN0)), Q2.1 (G), R20.2
C2: IC1.11 (PD7(AIN1)), Q1.1 (G), R21.2
EN_MOT: IC1.9 (PD5(T1)), Q3.1 (G), R19.2
EN_PWR: D1.2 (A), IC1.2 (PD4(XCK/T0))
EN_STB_HALL: IC1.26 (PC3(ADC3)), IC9.1 (VCC), IC10.1 (VCC)
GND: AC1.12 (GND_1), AC1.13 (GND_2), AC1.16 (GND_3), C1.2, C2.2, C3.2, C4.1, C5.1, C7.2, C8.1, C9.2, C10.2, C11.2, C12.2, C13.2, C14.1, C15.2, C16.2, C17.2, C18.2, C19.1, C20.2, C21.2, IC1.3 (GND), IC1.5 (GND), IC1.21 (GND), IC2.8 (GND), IC2.13 (!OE), IC3.2 (VSS), IC4.1 (GND), IC5.1 (TEMP), IC5.3 (GND), IC5.9 (EP), IC7.3 (GND), IC8.3 (GND), IC9.3 (GND), IC10.3 (GND), JP4.1, JP5.2, Q1.2 (S), Q2.2 (S), Q3.2 (S), Q4.2 (S), R12.1, R14.1, R19.1, R20.1, R21.1, R22.1, U$1.2 (G), U$1.4 (G), U$4.81 (GND), U$4.P1 (GND), U$4.P2 (GND)
HALL_LEFT: C18.1, IC1.24 (PC1(ADC1)), R13.2
HALL_RIGHT: C21.1, IC1.23 (PC0(ADC0)), R18.2
IRQ_ACC: AC1.11 (INT1), IC1.1 (PD3(INT1))
IRQ_NRF: IC1.32 (PD2(INT0)), U$4.71 (IRQ)
MEAS_UB: IC1.19 (ADC6), R16.2, R17.1
unnamed: C1.1, IC1.7 (PB6(XTAL1/TOSC1)), U$1.1 (X1)
unnamed: C2.1, IC1.8 (PB7(XTAL2/TOSC2)), U$1.3 (X2)
unnamed: C5.2, IC1.18 (AVCC), L1.2
unnamed: Q4.3 (D), R17.2
unnamed: C6.2, IC1.29 (PC6(/RESET)), R1.1, TP2.TP
unnamed: IC1.30 (PD0(RXD)), R2.2
unnamed: IC1.31 (PD1(TXD)), R3.2
unnamed: R4.1, U$2.11 (G/D), U$2.12 (G/D)
unnamed: R5.1, U$2.91 (B/G), U$2.92 (B/G)
unnamed: R6.1, U$2.21 (DP/DP), U$2.22 (DP/DP)
unnamed: R7.1, U$2.81 (C/F), U$2.82 (C/F)
unnamed: R8.1, U$2.31 (A/E), U$2.32 (A/E)
unnamed: R9.1, U$2.71 (E/A), U$2.72 (E/A)
unnamed: R10.1, U$2.41 (F/C), U$2.42 (F/C)
unnamed: R11.1, U$2.61 (D/B), U$2.62 (D/B)
unnamed: Q1.3 (D), U$2.101 (C1), U$2.102 (C1)
unnamed: Q2.3 (D), U$2.51 (C2), U$2.52 (C2)
unnamed: IC2.1 (Q1), R5.2
unnamed: IC2.2 (Q2), R6.2
unnamed: IC2.3 (Q3), R7.2
unnamed: IC2.4 (Q4), R8.2
unnamed: IC2.5 (Q5), R9.2
unnamed: IC2.6 (Q6), R10.2
unnamed: IC2.7 (Q7), R11.2
unnamed: IC2.15 (Q0), R4.2
unnamed: D2.2 (A), R23.1
unnamed: C4.2, IC1.20 (AREF), L2.1
unnamed: D3.1 (K), L2.2
unnamed: IC8.2 (OUT), R18.1
unnamed: D1.1 (K), D2.1 (K), IC3.3 (CE), R22.2
unnamed: LED1.A, R15.1
unnamed: IC5.7 (!CHRG), LED1.C
unnamed: JP2.1, Q3.3 (D)
unnamed: IC5.2 (PROG), R14.2
unnamed: IC7.2 (OUT), R13.1
SPI_ACC_CS: AC1.8 (!CS), IC1.12 (PB0(ICP))
SPI_MISO: AC1.7 (MISO), IC1.16 (PB4(MISO)), U$4.61 (MISO)
SPI_MOSI: AC1.6 (MOSI), IC1.15 (PB3(MOSI/OC2)), U$4.51 (MOSI)
SPI_NRF_CE: IC1.14 (PB2(SS/OC1B)), U$4.21 (CE)
SPI_NRF_CSN: IC1.13 (PB1(OC1A)), U$4.31 (CSN)
SPI_SCK: AC1.4 (SCLK), IC1.17 (PB5(SCK)), U$4.41 (SCK)
SR_CLK: IC1.28 (PC5(ADC5/SCL)), IC2.11 (SHCP), IC2.12 (STCP)
SR_DAT: IC1.27 (PC4(ADC4/SDA)), IC2.14 (DS)
STB_HALL_LEFT: IC1.22 (ADC7), IC10.2 (OUT)
STB_HALL_RIGHT: IC1.25 (PC2(ADC2)), IC9.2 (OUT)
USB_DTR: C6.1, IC4.13 (!DTR)
USB_N: IC4.6 (USB_N), JP4.2
USB_P: IC4.5 (USB_P), JP4.3
USB_RX: IC4.3 (RX), R3.1
USB_TX: IC4.2 (TX), R2.1
V+: AC1.1 (VDDI/O), AC1.14 (VS), C7.1, C8.2, C10.1, C12.1, C13.1, C14.2, C15.1, C19.2, C20.1, D3.2 (A), IC2.10 (!MR), IC2.16 (VCC), IC3.5 (VOUT), IC4.4 (V3), IC4.16 (VCC), IC7.1 (VCC), IC8.1 (VCC), Q4.1 (G), R12.2, U$4.11 (VCC)

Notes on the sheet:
10uH 15mA
4k6-280mA
INPUT CONNECTOR
USB TO SERIAL CONVERTER
BATTERY CHARGER
UB MEASUREMENT
BATTERY Sanyo UR14500 740mAh
3.3V LDO FOR 7SEGMENT, HALL, CH340, NRF, ACC
ATMEGA328
WIRELESS MODULE
DISPLAY
VIBRATION MOT.
ACCELEROMETER
PWR BY SOFTWARE
PWR WHEN USB CONNECTED

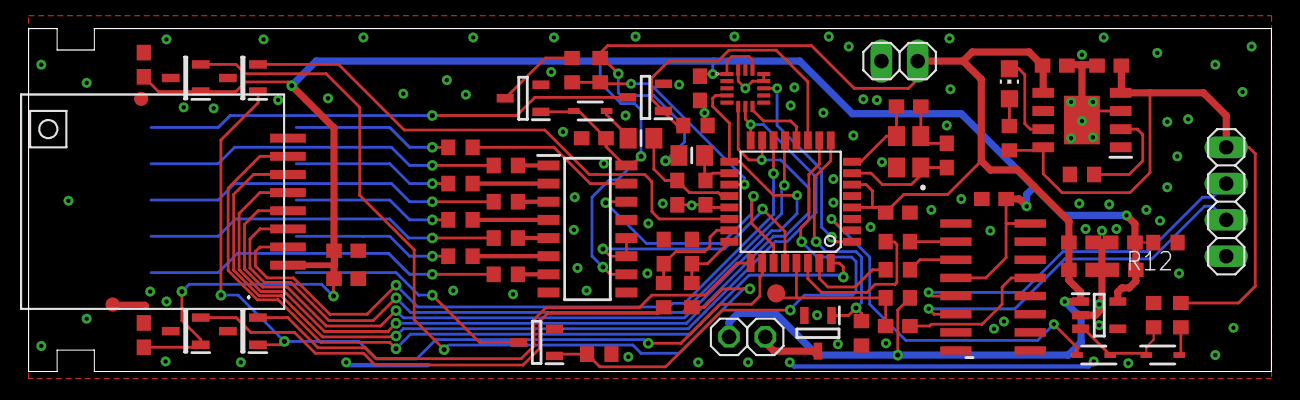
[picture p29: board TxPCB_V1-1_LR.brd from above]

Board: 2 copper layers, 87.0 x 24.0 mm, 72 parts (1 on the bottom side), 64 nets.

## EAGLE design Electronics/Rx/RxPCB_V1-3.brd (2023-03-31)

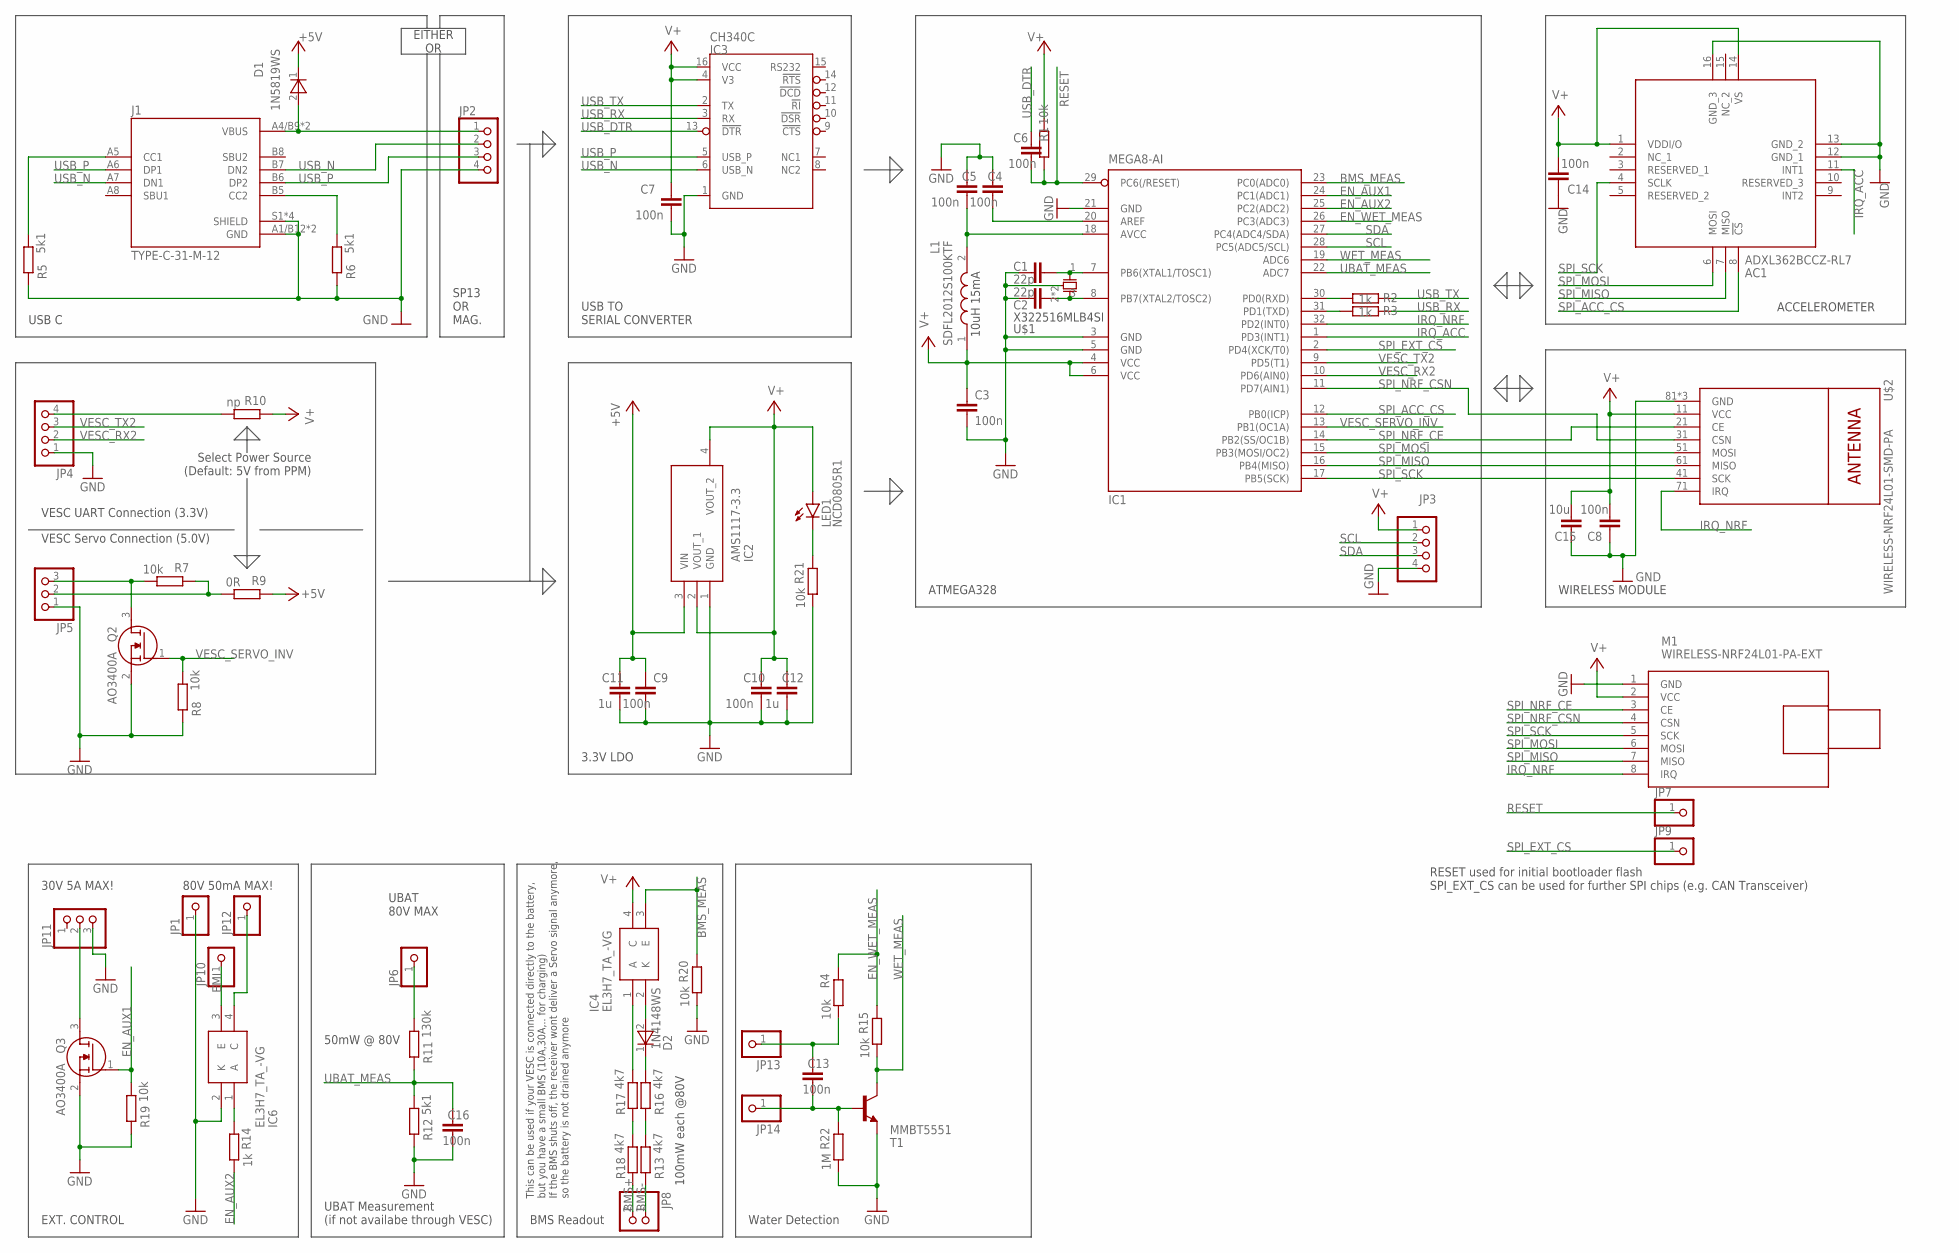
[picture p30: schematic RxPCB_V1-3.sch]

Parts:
AC1: ADXL362BCCZ-RL7; CC-16-4
C1, C2: 22p; C0603
C3, C4, C5, C6, C7, C8, C9, C10, C13, C14, C16: 100n; C0603
C11, C12: 1u; C0603
C15: 10u; C0603
D1: 1N5819WS; SODFL2512X90N
D2: 1N4148WS; SODFL2512X90N
IC1: MEGA8-AI; TQFP32-08
IC2: AMS1117-3.3; SOT229P700X180-4N
IC3: CH340C; SOIC16N
IC4, IC6: EL3H7_TA_-VG; SOIC127P700X200-4N
J1: TYPE-C-31-M-12; HRO_TYPE-C-31-M-12
JP1, JP6, JP7, JP9, JP10, JP12, JP13, JP14: PINHD-1X1; 1X01
JP2, JP3, JP4: PINHD-1X4; 1X04
JP5, JP11: PINHD-1X3; 1X03
JP8: PINHD-1X2; 1X02
L1: SDFL2012S100KTF; INDC2112X105N
LED1: NCD0805R1; CHIP-LED0805
M1: WIRELESS-NRF24L01-PA-EXT
Q2, Q3: AO3400A; SOT95P280X125-3N
R1, R4, R7, R8, R15, R19, R20, R21: 10k; R0603
R2, R3, R14: 1k; R0603
R5, R6, R12: 5k1; R0603
R9: 0R; R0603
R10: np; R0603
R11: 130k; R0603
R13, R16, R17, R18: 4k7; R0603
R22: 1M; R0603
T1: MMBT5551; SOT23-BEC
U$1: X322516MLB4SI
U$2: WIRELESS-NRF24L01-SMD-PA; WIRELESS-NRF24L01_SMD_PA

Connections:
+5V: C9.1, C11.1, D1.1 (K), IC2.3 (VIN), R9.1
BMS+: JP8.2, R18.1
BMS-: JP8.1, R13.1
BMS_MEAS: IC1.23 (PC0(ADC0)), IC4.3 (E), R20.1
EMI: IC6.3 (E), JP10.1
EN_AUX1: IC1.24 (PC1(ADC1)), Q3.1 (G), R19.2
EN_AUX2: IC1.25 (PC2(ADC2)), R14.2
EN_WET_MEAS: IC1.26 (PC3(ADC3)), R4.1, R15.1
GND: AC1.12 (GND_1), AC1.13 (GND_2), AC1.16 (GND_3), C1.2, C2.2, C3.2, C4.1, C5.1, C7.2, C8.1, C9.2, C10.2, C11.2, C12.2, C14.1, C15.2, C16.2, IC1.3 (GND), IC1.5 (GND), IC1.21 (GND), IC2.1 (GND), IC3.1 (GND), IC6.2 (K), J1.A1/B12 (GND), J1.B1/A12 (GND), J1.S1 (SHIELD), J1.S2 (SHIELD), J1.S3 (SHIELD), J1.S4 (SHIELD), JP1.1, JP2.4, JP3.4, JP4.1, JP5.1, JP11.3, M1.1 (GND), Q2.2 (S), Q3.2 (S), R5.1, R6.1, R8.1, R12.1, R19.1, R20.2, R21.2, R22.2, T1.E, U$1.2 (G), U$1.4 (G), U$2.81 (GND), U$2.P1 (GND), U$2.P2 (GND)
IRQ_ACC: AC1.11 (INT1), IC1.1 (PD3(INT1))
IRQ_NRF: IC1.32 (PD2(INT0)), M1.8 (IRQ), U$2.71 (IRQ)
unnamed: C1.1, IC1.7 (PB6(XTAL1/TOSC1)), U$1.1 (X1)
unnamed: C2.1, IC1.8 (PB7(XTAL2/TOSC2)), U$1.3 (X2)
unnamed: C5.2, IC1.18 (AVCC), L1.2
unnamed: J1.A5 (CC1), R5.2
unnamed: IC4.1 (A), R17.2
unnamed: IC1.30 (PD0(RXD)), R2.2
unnamed: IC1.31 (PD1(TXD)), R3.2
unnamed: D1.2 (A), J1.A4/B9 (VBUS), J1.B4/A9 (VBUS), JP2.1
unnamed: LED1.C, R21.1
unnamed: J1.B5 (CC2), R6.2
unnamed: IC6.4 (C), JP12.1
unnamed: JP4.4, R10.2
unnamed: JP5.2, R7.1, R9.2
unnamed: D2.1 (K), R16.2
unnamed: JP6.1, R11.2
unnamed: D2.2 (A), IC4.2 (K)
unnamed: C13.2, JP14.1, R22.1, T1.B
unnamed: C13.1, JP13.1, R4.2
unnamed: IC6.1 (A), R14.1
unnamed: R13.2, R16.1
unnamed: R17.1, R18.2
unnamed: C4.2, IC1.20 (AREF)
unnamed: JP11.2, Q3.3 (D)
RESET: C6.2, IC1.29 (PC6(/RESET)), JP7.1, R1.1
SCL: IC1.28 (PC5(ADC5/SCL)), JP3.2
SDA: IC1.27 (PC4(ADC4/SDA)), JP3.3
SPI_ACC_CS: AC1.8 (!CS), IC1.12 (PB0(ICP))
SPI_EXT_CS: IC1.2 (PD4(XCK/T0)), JP9.1
SPI_MISO: AC1.7 (MISO), IC1.16 (PB4(MISO)), M1.7 (MISO), U$2.61 (MISO)
SPI_MOSI: AC1.6 (MOSI), IC1.15 (PB3(MOSI/OC2)), M1.6 (MOSI), U$2.51 (MOSI)
SPI_NRF_CE: IC1.14 (PB2(SS/OC1B)), M1.3 (CE), U$2.21 (CE)
SPI_NRF_CSN: IC1.11 (PD7(AIN1)), M1.4 (CSN), U$2.31 (CSN)
SPI_SCK: AC1.4 (SCLK), IC1.17 (PB5(SCK)), M1.5 (SCK), U$2.41 (SCK)
UBAT_MEAS: C16.1, IC1.22 (ADC7), R11.1, R12.2
USB_DTR: C6.1, IC3.13 (!DTR)
USB_N: IC3.6 (USB_N), J1.A7 (DN1), J1.B7 (DN2), JP2.2
USB_P: IC3.5 (USB_P), J1.A6 (DP1), J1.B6 (DP2), JP2.3
USB_RX: IC3.3 (RX), R3.1
USB_TX: IC3.2 (TX), R2.1
V+: AC1.1 (VDDI/O), AC1.14 (VS), C3.1, C7.1, C8.2, C10.1, C12.1, C14.2, C15.1, IC1.4 (VCC), IC1.6 (VCC), IC2.2 (VOUT_1), IC2.4 (VOUT_2), IC3.4 (V3), IC3.16 (VCC), IC4.4 (C), JP3.1, L1.1, LED1.A, M1.2 (VCC), R1.2, R10.1, U$2.11 (VCC)
VESC_RX2: IC1.10 (PD6(AIN0)), JP4.2
VESC_SERVO_5V: JP5.3, Q2.3 (D), R7.2
VESC_SERVO_INV: IC1.13 (PB1(OC1A)), Q2.1 (G), R8.2
VESC_TX2: IC1.9 (PD5(T1)), JP4.3
WET_MEAS: IC1.19 (ADC6), R15.2, T1.C

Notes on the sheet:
10uH 15mA
USB C
3.3V LDO
ATMEGA328
WIRELESS MODULE
EXT. CONTROL
ACCELEROMETER
USB TO SERIAL CONVERTER
SP13 OR MAG.
EITHER OR
VESC UART Connection (3.3V)
VESC Servo Connection (5.0V)
Select Power Source (Default: 5V from PPM)
UBAT 80V MAX
50mW @ 80V
UBAT Measurement (if not availabe through VESC)
30V 5A MAX!
80V 50mA MAX!
Water Detection
RESET used for initial bootloader flash SPI_EXT_CS can be used for further SPI chips (e.g. CAN Transceiver)
BMS Readout
100mW each @80V
This can be used if your VESC is connected directly to the battery, but you have a small BMS (10A,30A,.. for charging) If the BMS shuts off, the receiver wont deliver a Servo signal anymore, so the battery is not drained anymore

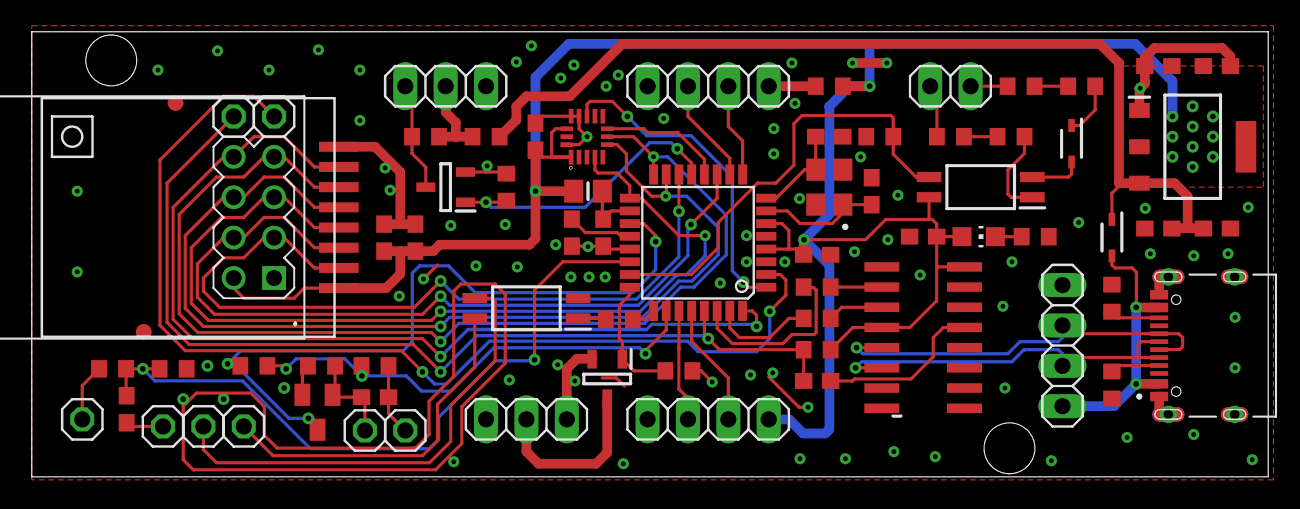
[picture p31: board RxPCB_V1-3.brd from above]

Board: 2 copper layers, 77.8 x 28.0 mm, 69 parts (0 on the bottom side), 56 nets.

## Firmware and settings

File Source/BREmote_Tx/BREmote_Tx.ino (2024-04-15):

/* When flashing fails, select Processor: Aruino Nano (OLD BOOTLOADER)*/
/* When flashing fails, select Processor: Aruino Nano (OLD BOOTLOADER)*/
/* When flashing fails, select Processor: Aruino Nano (OLD BOOTLOADER)*/

/*
    BREmote Tx
    Copyright (C) 2022 Ludwig Brechter (contact@lbre.de)
    
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
    You should have received a copy of the GNU General Public License
    along with this program.  If not, see <http://www.gnu.org/licenses/>.
 */

#include "BREmote_Tx.h"

RF24 radio(NRF_CE, NRF_CSN); // CE, CSN

void setup() 
{
  enableSerial();
  initReg();
  initPins();
  initNRF();
  initEEPROM();
  setupTimer2();
  enablePower();
  #ifdef NO_LOCK
    system_locked = 0;
  #endif
  delay(1000);
  enableDisplay();
}

void loop() 
{
  checkLastActivity();
  checkBattery();

  if(poweroff)
  {
    powerOffAnimation();
    digitalWrite(EN_MOT, LOW);
    sleepUntilMovement();
  }
  else
  {
    if(system_locked)
    {
      displayLock();
    }
    else
    {
      if(comm_errors < 100)
      {
        if(remote_error)
        {
          displayError(remote_error);
          blinkDot |= 0x04;
        }
        else
        {
          blinkDot &= 0xFB;
          #ifdef SHOW_TEMP
            if((millis() / 2000 ) % 2)
            {
              displayIdle(2);
            }
            else
            {
              displayIdle(3);
            }
          #else
            displayIdle(2);
          #endif
        }
      }
      else
      {
        displayError(err_cause);
      }
    }
    checkToggleButton();
  }
  delay(10);
}

ISR(WDT_vect) 
{ //Leave empty
}

ISR(TIMER2_COMPA_vect)
{
  if(isr_active)
  {
    multidiv++;
    if(multidiv > 20)
    {
      if(motordiv >= 10)
      {
        if(blinkDot)
        {
          #ifdef MOTOR_ENABLED 
            digitalWrite(EN_MOT, HIGH);
          #endif
          mot_active = 1;
          motordiv = 0;
        }
      }
      else
      {
        motordiv++;
        digitalWrite(EN_MOT, LOW);
        mot_active = 0;
      }
      //1Hz
      multidiv = 0;
      blinkDotRoutine();
    }
    //if(comm_errors >= 250 && multidiv % 10) sendValues();
    
    displaystate ^= 1;
    updateDisplay();
    measureAndBuffer();
    calcFilter();
    //if(comm_errors < 250) sendValues();
    sendValues();

    // adjust softpower counter
    if (++soft_power_counter > soft_power) {
      if (soft_power_steps < 0) soft_power_steps++;
      if (soft_power_steps > 0) soft_power_steps--;
      soft_power_counter = 0;
    }
  }
}

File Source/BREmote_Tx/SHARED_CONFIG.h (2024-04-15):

/*
    BREmote Shared Config File
    Copyright (C) 2022 Ludwig Brechter (contact@lbre.de)
    
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
    You should have received a copy of the GNU General Public License
    along with this program.  If not, see <http://www.gnu.org/licenses/>.
 */

/*
 * This is the only file a user should make changes
 */
#error "Please change the adresses below to someting unique for your setup!! Do so both in Tx and Rx SHARED_CONFIG.h! Then delete this line"
//These Adresses need to consist of exactly 5 letters or numbers
uint8_t rxAddr[6] = {"BREAI"}; //From Rx To Tx (Board to Remote)
uint8_t txAddr[6] = {"BREAO"}; //From Tx To Rx (BRemote to Board)

//Output Debug Information
  #define DEBUG
  
  //#define STEERING_ENABLED                    //If steering feature is enable (see also fine tuning at "Tx Specific")
  //#define REVERSE_ENABLED                     //Puts remote into reverse mode: Only two "gears": Forward (F) and Reverse (P)
                                                //Important: Also update RX! Otherwise in failsafe the VESC will be sent wrong commands!
/*
 * Tx Specific
 */

    //Behaviour of the User Interface
      //#define NO_LOCK            //No locking function, as soon as remote is on, throttle is active
      //#define NO_POWERBUTTON     //The toggle button cant turn off the remote (the remote will power off automatically if the receiver is off for > NO_ACTIVITY_TIMEOUT (see below))
      //#define NO_GEARS           //Gears can't be switched (set STARTGEAR to 9)
      //#define THR_TO_PWRUP       //If throttle also needs to be pushed to power the remote (helps if remote turns powers up on its own)
      //#define DONT_SEND_IDLE     //If the remote should send packets in idle (no trigger applied), contiues for a short time set by TOGGLE_BLOCK_TIME
                                  //Useful, if 2 or more people have one remote each and control the same towboogie
          
      #define STARTGEAR 0         //The gear that is set after poweron or unlock (0 to 9)

      #define SHOW_TEMP           //If display should also show temp (alternate btw. temp and bat) or only show bat
      
    // Hyteresis
      #define TOG_DIFF 8                          //Hysteresis for Toggle (30 for toto)
      #define TOG_STB_DIFF 8                      //Hysteresis for Standby Toggle (30 for toto)
      #define THR_STB_DIFF 10                     //Hysteresis for Standby Throttle
      
    // Steering Feature (e.g. for tow boogies) - Enable at top of this file
      #define STEER_TOG_DIFF 15                   //Sensitivity of Steering
      #define STEER_DEADZONE 3                    //Deadzone for steering
      #define TOGGLE_BLOCK_TIME 500               //How long toogle button is in steering (*10ms)
    
    //Timings
      #define UNLOCK_TRIGGER_TIMEOUT 5000         //Time after unlock until trigger times out (ms)
      #define LOCK_PWR_WAITTIME 2000              //Time toggle needs to be pressed to power off or lock system (ms)
      
      #define GEAR_CHANGE_WAITTIME 100            //Time toggle needs to be pressed to change gear (ms)
      #define GEAR_DISPLAY_TIME 1000              //How long the new gear is shown (ms)

      #define ERR_DELETE_TIME 2000                //How long the "E-" is shown after deleting an error. In this time, the user can also change gear, even if the error is still persistent (and therefore will be shown again after this time is over)
    
      #define NO_ACTIVITY_TIMEOUT 60000           //Turn off power if no button is pressed and receiver has no connection (ms)
    
    //Internal Battery measurement
      #define INT_VBAT_CALIBRATION 0.004290224    //This converts ADC Bits to Voltage
      #define INT_VBAT_FULL_AT 410                //Voltage at which 100% internal Battery is displayed (100*V) DEFAULT 410
      #define INT_VBAT_EMPTY_AT 340               //Voltage at which 0% internal Battery is displayed (Also the protection limit), MIN: 34V (100*V) DEFAULT 340
      #define FOIL_VBAT_WARN_AT 10                //Percent at wich VESC Battery triggers a warning (%)
    
    //For Debug, Viration Motor can be disabled
      #define MOTOR_ENABLED


#ifdef REVERSE_ENABLED
  #define MAX_GEARS 2
  #define STARTGEAR 1
#else
  #define MAX_GEARS 10
#endif
/*
* Error Codes (don't change)
*/
#define ERR_PACKET_CONTENT 3
#define ERR_NO_ACK 4
#define ERR_EEPROM 5
#define ERR_NRF 6
#define ERR_WET 7
#define ERR_BMS 8

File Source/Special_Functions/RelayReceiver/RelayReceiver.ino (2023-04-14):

/*
    BREmote V1.1
    Copyright (C) 2022 Ludwig Brechter (contact@lbre.de)
    
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
    You should have received a copy of the GNU General Public License
    along with this program.  If not, see <http://www.gnu.org/licenses/>.
 */

/*
* This sketch can be used to monitor the VESC Parameters of a BREmote Receiver
* (with VESC_RELAY_MODE enabled), wirelessly (e.g. for friends outside of the water)
*/

#include <SPI.h>
#include "RF24.h"

#include "datatypes.h"
#include "buffer.h"
#include "crc.h"


RF24 radio(10,7);

byte addresses[][6] = {"BREAI","BREAR"};

float fetTemp = 0;
float motCur = 0;
float batCur = 0;
float duty = 0;
float batVolt = 0;

void setup() {
  Serial.begin(9600);
  
  radio.begin();
  radio.setPALevel(RF24_PA_HIGH);
  radio.setDataRate(RF24_250KBPS);
 
  radio.enableDynamicPayloads();
  radio.enableAckPayload();
  radio.setRetries(2,1);

  radio.openWritingPipe(addresses[0]);
  radio.openReadingPipe(1, addresses[1]);

  radio.startListening();  // put radio in RX mode

  Serial.println("Tfet,Imot,Ibat,Duty,Ubat");
  Serial.println("Tfet,Imot,Ibat,Duty,Ubat");
}

uint8_t message[25];

void loop() 
{
  if( radio.available() )
  {
    uint8_t rxArr[25];
    radio.read( &rxArr, sizeof(rxArr));
    
    if(rxArr[0] == 2 && rxArr[rxArr[1]+4] == 3)
    {

      uint16_t crcMessage = 0;
      uint16_t crcPayload = 0;
  
      crcMessage = rxArr[rxArr[1]+2] << 8;
      crcMessage &= 0xFF00;
      crcMessage += rxArr[rxArr[1]+3];
  
      //Extract payload and also calculate CRC
      memcpy(&message,&rxArr[2],rxArr[1]);
  
      crcPayload = crc16(message, rxArr[1]);
      
      if(crcPayload == crcMessage)
      {
        int32_t cnt = 5;
        if(rxArr[1] == 19)
        {
          //Serial.println("Tfet,Imot,Ibat,Duty,Ubat");
          
          fetTemp = buffer_get_float16(message, 10.0, &cnt);
          motCur = buffer_get_float32(message, 100.0, &cnt);
          batCur = buffer_get_float32(message, 100.0, &cnt);
          duty = buffer_get_float16(message, 10.0, &cnt);
          batVolt = buffer_get_float16(message, 10.0, &cnt);

          //String sprt = "Fet Temp: " + String(fetTemp) + "°C, Mot. Curr.: " + String(motCur) + "A, Inp. Curr: " + String(batCur) + "A, Duty:: " + String(duty) + "%, Volt: " + String(batVolt) + "V";
          //String sprt = String(fetTemp) + "," + String(motCur) + "," + String(batCur) + "," + String(duty) + "," + String(batVolt);
          //Serial.println(sprt);
        }
        if(rxArr[1] == 9)
        {
          fetTemp = buffer_get_float16(message, 10.0, &cnt);
          batVolt = buffer_get_float16(message, 10.0, &cnt);

          //String sprt = "Fet Temp: " + String(fetTemp) + "°C, Volt: " + String(batVolt) + "V";
          //Serial.println(sprt);
        }
      }
      else
      {
        Serial.println("CRC NOK");
      }
    }
  }
  delay(100);

  String sprt = String(fetTemp) + "," + String(motCur) + "," + String(batCur) + "," + String(duty) + "," + String(batVolt);
  Serial.println(sprt);
}

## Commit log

2023-03-12 Implement Wetness Sensor Function
    Also renamed folders and file names
    to not contain version number anymore.
2023-03-20 Add BMS Monitoring, Fix Wetness Sensor
    - Added BMS Monitoring in Source
    - Fixed Wetness Sensor (EMI resiliance)
    [RxPCB_V1-2.brd, RxPCB_V1-2.sch]
2023-03-29 Add timeout to error display
    In order to allow the user to change gear during an error, a timeout is introduced.
    [BREmote_Tx.h, HALL.ino, SHARED_CONFIG.h]
2023-03-31 Add analog UBAT meas and add connection info to Readme
    [Readme]
    - Added connection diagrams
    [Source]
    - Made connection to VESC UART optional (defined in SHARED_CONFIG)
    - Added analog UBAT measurement
    [Electronics - Rx]
    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
    [RxPCB_V1-3.brd, RxPCB_V1-3.sch]
2023-04-14 Increase NRF interrupt-to-readout delay
2023-04-20 Add compiler error if address is not changed, increase tolerances on some values
    [Communication.ino, SHARED_CONFIG.h]
2023-04-20 Important fix: Disable MOSI Pin (could damage battery in standby)
    [System.ino]
2023-04-23 Add longrange (LR) and steering functionality
    Add a longrange (LR) version of Tx board
    Add steering functionality in code
    [TxPCB_V1-1_LR.brd, TxPCB_V1-1_LR.sch]
2023-05-05 Add "TOTO-Mode", Disable Lock&Poweroff when Throttle is active
2023-06-01 UI Overhaul
    Remove Toto Mode
    Add more options to customize UI:
    - NO_LOCK
    - NO_POWERBUTTON
    - NO_GEARS
    Add temperature display
    [Antenna1.stl, Antenna2.stl, MagRodStopper_+04_more_2x.stl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]
2023-10-02 Add softer gears
    - Softer Gears: When at full throttle, changing gear is smoothened (Thanks to Dyse)
    - Added Information how to connnect ISP for LR version
2023-10-17 Add improved LR bodies
    [Antenna1.stl, Antenna2.stl, MainBody_Left_2m.stl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]
2023-12-28 Update of LR main body housing
    - Longer antenna hole (now 58mm)
    - Reinforcements
    [Main_Body_left_normal.step, Main_Body_right_toggle_protection.step, main_body_left_normal.stl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]
2024-04-15 Release V1.7
    Note: Changing to this release will require new calibration!

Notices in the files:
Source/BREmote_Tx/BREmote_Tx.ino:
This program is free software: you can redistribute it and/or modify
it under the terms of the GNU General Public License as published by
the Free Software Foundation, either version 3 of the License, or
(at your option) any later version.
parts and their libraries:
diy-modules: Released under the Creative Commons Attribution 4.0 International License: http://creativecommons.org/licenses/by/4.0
